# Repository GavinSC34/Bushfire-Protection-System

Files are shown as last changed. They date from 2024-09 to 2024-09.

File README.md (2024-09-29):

## Bushfire Protection System 👋

Climate change challenges homeowners to face the reality of increasingly frequent and
intense bushfires. To avoid major loss of life, the advice from the fire service, police and planners
is to evacuate. Take what you can, leave your house, and hope fire fighters can cope. And often,
they can't cope. 

The project aims to protect the house from bushfire when you are told to leave.
Spraying systems can be activated, by the homeowner, or automatically.
Loss of mains electricity and internet is common in major fires and is addressed.

Temperature and smoke sensors, as well as press button and Blynk, can start spraying.

The author lives in a rural area of Tasmania, Australia. He was a volunteer fire fighter for 15 years
and worked extensively on fire safety for the home through a community fireguard program.

In Australia and many other countries, rural residents rely on tank water. Many have limited water to fight fires and probably don't have ‘off the grid’ solar power available. Your situation might be different of course, you might even have the luxury of a piped, good pressure, water supply. 



A deep cycle battery and 12 volt pump is used to spray water around the house. Since a small pump has limited capacity, a micro-controller sequentially controls a number of spray or sprinkler lines. A number of ‘triggers’ are built into the controller. The triggers utilise temperature and smoke sensors programmed to automatically start the pump at critical thresholds: 

• high temperature 

• sudden rise in temperature 

• heavy smoke 

• elevated temperature plus smoke 

As well, the system can be started by 

• a start switch (‘start and run’ switch) 

• a smart phone app switch linked to the system via the home WiFi and thus the internet. 

If the WiFi is unavailable the sensors will still work automatically. The phone app also shows the temperature and smoke, allowing monitoring from many kilometres away – provided the WiFi is working and the internet is available. Phone towers have been disabled in past major bushfires. While a 12v system is designed for the 240v power supply going down, you may want to consider an arrangement that can start on 240v and switch to 12v only if needed. This refinement is not included here (the simplest option may be adding a 240v battery charger).

Another useful addition would be an ESP32-CAM sending photos to Blynk.

Development of the concept is welcomed.

---------------------------------------------
<i>What will it cost? </i>

Each situation will be different. For those with off-grid power and a large dam, there is less infrastructure. Much of the work involves siting sprinklers, leading hoses to them, and fitting solenoid valves and wires. The micro-controller costs are surprisingly low but learning to code Arduino boards and the Blynk phone app is a steep learning curve for those not immersed in IT. The code is freely available as an example.

<i>Is it worth doing?</i>

While an automated spray/sprinkler system cannot guarantee your home will survive a bushfire, it should certainly improve your chances. With climate change and more forceful evacuation messages it should provide better peace of mind, if not save your situation. Do you have to evacuate? Legally, in most Australian jurisdictions, the answer is no. However it is usually the safest option if done early. Consider not only your safety, but the safety of fire fighters.

<i>How good is the science?</i>

The short answer is, it’s early days. Smoke sensors have been around for years and are utilised in building fire systems and smoke alarms. Temperature sensors are likewise proven items, as anyone with a home weather station can attest. Micro-controllers drive anything from washing machines to coffee makers. Phone apps are ubiquitous. What isn’t known is what level to set the ‘triggers’. How long to spray for? Will it be enough water in high wind? What can go wrong in your situation? The battery will pump continuously for maybe an hour, longer with intermittent pumping. Is that enough? Will the electronics be robust enough? All these can be considered however, and adapted to your situation. Plus, we need many installations and many tests before final guidelines can be provided. 

<b>Water</b>

Properties without a reliable water supply will need a water tank. A 4600 litre tank, minimum, is suggested for a small to medium sized house. More water is needed to protect sheds and outbuildings. The tank(s) are best dedicated to fire safety in the summer. 

<b>Hardware for water distribution</b>

SEAFLO 55 Series Water Pressure Pump (12V/5.5GPM/60PSI) (20.8LPM/413Kpa) $224, Amazon

Century Deep Cycle Battery N70T 102 Amp-hour 
https://www.supercheapauto.com.au/p/century-century-deep-cycle-battery-n70t-102ah/602320.html     $252

Solar panel and charger
https://www.supercheapauto.com.au/p/ridge-ryder-ridge-ryder-solar-panel-kit---110-watt/610689.html $149 

12V DC 1/2" Water Solenoid Valves - Normally Closed https://www.amazon.com.au/gp/product/B07SB3SGDY/ref=ppx_od_dt_b_asin_title_s00?ie=UTF8&psc=1 $8.47 each

IN4007 ‘flyback’ diodes. To protect the circuit from voltage spikes when the solenoids are activated. This forum article explains why and how to connect them up: 
https://forum.arduino.cc/t/flyback-diode-required-for-relay-board-and-12v-solenoid/422993/6
Available from Little Bird Electronics or Jaycar.

0.5mm Multi-Core Irrigation Cable
https://sunshoweronline.com.au/multi-core-irrigation-cable-0-5mm/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
9 Core Irrigation Cable 0.5mm costs $2.85 per metre.  3 core costs $1 per metre. You will probably need a mix.

Sprinkler capable of covering approximately 450 to 500m². 
Holman 15mm Metal Impact Sprinkler Head, Bunnings
https://www.bunnings.com.au/holman-15mm-metal-impact-sprinkler-head_p3110996
$24.55 OR,
VYRSA 35 3/4" Brass Full-Circle Impact Sprinkler Dural Irrigation $52.58
https://duralirrigation.com.au/products/vyrsa-35-3-4-brass-full-circle-impact-sprinkler
This second sprinkler promises better performance with the above pump and an 18mm (¾”) supply hose, according to it’s specifications.

<b>Pipe and Hose</b>
How many of each? Maybe you need two systems, one for the house, the other for the sheds. That’s two pumps, two batteries and maybe onesolar panel and charger. The example house has four impact sprinklers and solenoids for them, plus three spray/mist lines and solenoids for each hose line. Connecting wire depends on distance from the pump and battery and how many ‘arms’ the system has. The sheds will have a similar arrangement.

It’s worth testing to see what hose works. Garden hose is 12mm, but 18mm is preferable for getting a volume of water over a long run. See https://www.bunnings.com.au/holman-18mm-x-30m-yardmate-garden-hose_p0047705. 30m costs $80. Maybe you have a short run and 12mm hose works. That’s fine, and cost is $20 to $30 for 30m. Map it out. Polypipe is often the best solution although joins aren't quite as easy as garden style hose. If you have 1 inch input and output on your pump, use 1 inch polypipe for delivery. Bury the hose line.

If you put the solenoids near the pump and not at the end of the hose line, and have one line for every sprinkler or sprayer you will save on wire, but may need more hose. The mist spray lines use 13mm black poly pipe with a spray every metre or so. If you have a lot of spray outlets on the line, it requires a lot of water.

<b>Micro-controller and related parts</b>

The suggested controller is a Lonely Binary ESP32-S3, $30. This model has an external antenna. It also comes supplied with enough solderable pins to mount the unit on a breadboard or PCB.
https://www.amazon.com.au/Development-Bluetooth-Espressif-ESP32-S3-DevKitC-1U-N16R8-Micropython/dp/B0CKYRGHBD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

8 Channel relay to handle 12v, $21.95 at Jaycar.
https://www.jaycar.com.au/arduino-compatible-8-channel-relay-module/p/XC4418
Automotive Fused Relay SPST 30A, 12.95 Jaycar
https://www.jaycar.com.au/automotive-fused-relay-spst-30a/p/SY4077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
The 12v water pump has a high electrical load, particularly when starting up. This heavy duty relay connects the positive from the deep cycle battery to the positive of the pump. When the micro-controller ‘pump’ relay is activated it in turn switches this one. (Two relays piggy-backed). Heavy duty wiring can thus be fully employed between the battery and the pump.

Power supply regulator, 12v to 5v. Arduino Compatible DC Voltage Regulator Module CAT.NO: XC4514 Jaycar $10.25. Different regulators were tried and some failed, ruining parts. This one has proven to be stable. 
https://www.jaycar.com.au/arduino-compatible-dc-voltage-regulator-module/p/XC4514
Temperature sensor TMP36 - Analog Temperature sensor, Little Bird Electronics $5.80 https://littlebirdelectronics.com.au/products/tmp36-analog-temperature-sensor-tmp36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 Note that different sensors, even in the same TMP36 package, can have the anode and cathode reversed. Check the data sheet carefully and don’t get them mixed up.
MQ-2 smoke sensor module, Little Bird Electronics $9.66.
https://littlebirdelectronics.com.au/products/mq-2-smoke-sensor-module?_pos=2&_psq=smoke&_ss=e&_v=1.0

Resistors, 1/4w: 220 ohm, 10K ohm.

LED. Little Bird has a selection.

Push button switch. Little Bird has a selection.

Jumper wire F/F to neatly connect the circuit to the sensors and relays. 
https://littlebirdelectronics.com.au/products/40-pin-15cm-jumper-wire-f-f?_pos=27&_sid=7b3ef1029&_ss=r gives flexible choice, $6.36.

Solderable breadboard, Core Electronics, $9.80.
https://core-electronics.com.au/solder-able-breadboard.html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

Circuit diagram:


<b>PCB</b>

KiCad was used to design a PCB and SeeedStudio to make a it. A unit that lives out in the weather, even if it is in a plastic box, will be prone to corrosion. Since there is a lot at stake, everything to be as reliable as you could make it.
If your needs just happen to be close to this design, there are a few spare PCB boards available. However most situations will be different – the number of lines, available power and so on.

<b>The External Circuitry</b>

The example follows the circuit suggested by LarryD in the flyback diode post mentioned above, https://forum.arduino.cc/t/flyback-diode-required-for-relay-board-and-12v-solenoid/422993
The major difference is the inclusion of an 8 channel relay. (Jaycar provides a datasheet for this, item XC4418.) Note that the centre terminal on each channel connects to the +ve, and the leftmost terminal will carry that positive to the solenoid once the relay is activated.

In the example build the ESP32, buck converter (or voltage regulator) and relays are all housed in one box, but the wiring is almost the same. <i>Important difference: an eight channel relay takes 12v, so the black and red wires to the relay will come from the battery end of the buck converter.</i> Jaycar one to four channel relays use 5v as shown here.



Attrib: LarryD.

For eight channels the wiring to each solenoid is repeated. The detailed illustration below shows the eight channel hookup, the horizontal red +ve wires are connecting each centre pin. The lower red wires, when switched, will take the +ve to the solenoids or the pump. The dark plugs at the bottom are waterproof connectors. Note this is not automotive style +ve and -ve wiring in the connectors.



<b>Bushfire behaviour</b>

Bushfire attack essentially takes five forms:

• <b>Wind:</b> Strong winds resulting from severe bushfires will drive embers into vulnerable areas of a building, preheat and dry fuel ahead of a fire, lift roofing and extend flames along a more horizontal plane closer to building elements.
    
• <b>Smoke:</b> While smoke will cause minimal damage to property, it can severely affect the health of residents. Smoke is a significant factor in at risk developments, particularly where residents are susceptible to respiratory disorders. Smoke can also reduce visibility during evacuation or shelter situations.
    
• <b>Embers:</b> Ember attack is responsible for most bushfire related building fires. Embers can also cause spotting in advance of the bushfire and ignite building elements.
    
• <b>Radiant heat:</b> Radiant heat can severely impair the health of residents and the integrity of building elements. Radiant heat can prevent emergency services personnel assisting occupants of at risk developments.
    
• <b>Flame:</b> Flame attack will severely restrict fire fighting operations, resulting in the ignition of building elements and a threat to the health of residents and their capacity to evacuate the area.
    
-– NSW Rural Fire Service, https://www.rfs.nsw.gov.au/plan-and-prepare/building-in-a-bush-fire-area/what-you-need-to-know/decision-tree-pages/goal-13

Your system
Planning your system requires you to carefully evaluate how to respond to each of those elements of bushfire behaviour.

<b>Wind:</b> you should be aware of your most likely wind direction for bush fire. Gale-force hot winds, which way do they come? What’s affecting the direction? Valleys, trees, vegetation? That side of your house may need more water. If you get the chance, set up a sprinkler next high fire danger day and see what it does. Think about wind carrying your water spray away from where it will be effective. How long will it take to dry that side of your house if you do spray it? How long does it take to wet it down?

<b>Smoke:</b> isn’t going to burn your house down, but is a warning and thus a trigger for your system. You can have intense smoke from kilometres away, think about how that might work. Really intense pungent smoke is usually an indication that a fire is on top of you. If you have limited water, that should be your trigger. You might use a beekeeper’s smoker to calibrate my system.

<b>Embers:</b> the peril of eucalyptus forests. Consider your house from top to bottom. The example situation has a Colourbond roof and vertical board walls. There is a fine mesh gutter guard in all the buildings’ gutters – for keeping leaves and embers out of the gutters and also to keep leaves out of the water tanks. To cool the boards and windows there ise a fine mist line high up the walls and running all the way around the house. This also serves to add to the accumulated water at the foot of the walls, because that is where smouldering or even burning leaves will gather. Further out, there are the heavy duty sprinklers spraying in an arc to saturate the closer trees, shrubs, lawns and walkways.

<b>Radiant heat:</b> what fuel is near the house? Remove flammable trees or have enough water and spray power to wet them down. Imagine your favourite gums on fire, up their bark and in their crowns. Don’t have an avenue of such trees around your house, particularly on the fire weather side, separated trees are better. Look at the trees for wind protection (needed) and trees as fuel (a problem). It’s a tricky balance that has to be addressed. Also look at adjacent sheds or buildings. Can they catch alight? Look to your windows, how might they be affected?

<b>Flame:</b> is what we are trying to avoid. Wet, cool surfaces don’t burn. However the extremes of bushfires make it hard to plan for a fire sequence. It might be ember attack, then fire front, then ember attack for hours following. It might be fire front first! Your system has to cope with the possibilities.

The example installation is set up to spray a sequence of a minute each, heavy sprinkler, then mist line, then next heavy sprinkler, then next mist line, working around the house. It was checked it out on a high fire danger day with strong hot winds and everything around the house looked flooded. A sequence lasts about seven minutes, then will start again if smoke and temperature trigger it, or if set going through the phone app. 
<TABLE BORDER=5><TBODY>  <TR>
    <TH>More on bushfires</TH>
<TD>Doing Community Fireguard work for Tasmanian Fire Service some years ago, a number of older residents talked about their experiences in the 1967 fires – still considered one of the worst ever – and later fires. Here are three observations: “The winds were 100 miles an hour, the temperature 100 degrees [ºF], and the dams were all empty!” (Ted Domeney. talking about 1967.) “I watched the embers flying across the Channel and saw the fires start up on Bruny Island. There were fireballs, burning balls of gas, blowing over the water.” (Colin Glanville, talking about 1967.) “The big gum outside the house had burnt and the heat had cracked the upstairs window. Sparks blew in and a chair was smouldering. Luckily we got back just in time.” (Ridgeway resident, talking about 1998). Ideally, your house, and windows, should be cool and wet enough to survive. Bushfires can be extreme, and quirky.</TD></TR> 
</TBODY></TABLE>
Now look again. Heat travels upwards. On the leeward side of this house there is a hill that falls away. Unfortunately it has many gums and wattles. After a fire front has passed that area may take a while to be set off by embers, but when it gets going it will be very hot, burning hard, uphill, right towards the house. Are you exposed?

<b>Arduino on the trigger</b>

The automated part of the system involves the micro-controller (an Arduino ESP32 model in my case), programmed to start the pumping sequence when:

• the temperature is over 45º C. Rationale: a 35 to 40º C day is not uncommon for fire weather, plus the sensor is in a box. The box is ventilated to allow air (and smoke) to move through it but an elevated temperature is expected. Then a fire will add to that.

• the smoke is more than 4000 ppm. Rationale: calibrated by passing smoke over the sensor. Also checked using the gas from a cigarette lighter held close to the sensor.

• the smoke is more than 2500 ppm AND the temperature is over 45º C. Rationale: a fire could be approaching in lower temperature and the wind is not blowing intense smoke over the unit yet. Smoke and heat together should be a useful trigger.

• the temperature increases 4º C in a sudden ramp. Rationale, an approaching fire might raise heat more or less steadily above the ambient hot day temperature, even on a 25º C day. Any weather hotter than 20º with winds more that 20 knots plus low humidity can be bad fire weather. (The 20/20 rule.) The system takes an average of a ten second period (call this a decade) and compares it against the decade just before, and just before that, looking back over the past nine decades.

These figures have not been tested in a bush fire! We need many units and some real world experience to add to the science. The example system will monitor the sensors through the coming summer so as to add to our knowledge and fine-tune the estimates. 

<b>Finger on the trigger</b>

It may be that your local radio, fire brigade or community fireguard alert you to an approaching fire. Fires start somewhere, you might be unlucky and it starts near you. Throw your valuables into the car, turn on the system and press the button. The spray should be working as you drive away to your evacuation centre. After one full spraying sequence it will stop. But the sensors are there waiting; as it’s triggered it will start another sequence.

<b>Blynk on the trigger</b>

Micro-controllers are readily connected to WiFi. Some units can be connected to the mobile phone network in 4G or 5G. This system is based on the house WiFi and the unit can send and receive information over the internet. Blynk (https://blynk.io/) provides a fairly easily built system to allow Arduino style programs to interact with a phone app or via a computer. The app includes a button to start the system at a distance, and a monitor to see if it has already started due to one of the other triggers.

If the power to the house is lost so is the WiFi – unless there is time to change the modem to battery, where it will continue to connect to the internet via 4G. (No fibre optic NBN here, but at least we have moved up from ADSL+.) Since the system is on a 12 v battery, the Arduino should keep communicating.



The app, and the start button, are useful for testing the system –  especially to check if program changes work correctly.

<b><i>Part 2 – Software and Communication></i></b>

<i>Arduino to PCB – a steep learning curve</i>

A number of people have expressed interest in the system, but were daunted by having to learn electronics and programming. This section explains a little of what is involved - those already conversant with Arduino programming, OTA, circuit design and board making etc may skip this section. 

If you don’t like the idea of soldering and programming, you might find someone in your family or community who is willing to take this on. The plumbing of the hose lines is something most people can do.

The internet has great resources for training videos and discussion. The Arduino and Blynk websites have very useful introductions. Jaycar and other product supplier websites have not only Arduino compatible products, but also specification sheets explaining how to wire up the item and use it with a micro-controller. The Arduino IDE makes programming very straight-forward.

<b>Arduino</b>

As of February 2020, the Arduino community included about 30 million active users based on the IDE downloads. 
-– https://en.wikipedia.org/wiki/Arduino

Arduino micro-controllers have been available for nearly 20 years and their programming and utility is very well developed. They have a reputation for reliability. The ‘integrated development environment’ handles the programming aspect, with a programming language check, upload to the Arduino board facility and a comprehensive library of ready to run software called ‘sketches’ – and much more.

For those interested in the challenge of learning to build projects and program the Arduino, or compatible devices of other brands, there are excellent learning resources online, including beginners courses. Paul McWhorter’s Arduino Lessons (https://toptechboy.com/arduino-lessons/) are comprehensive and entertaining. Although I must admit I’m still a novice programmer.

I was given an Arduino Uno to ‘start playing with’; thanks Gene. I blew it up after a few weeks by powering it from an external source, then, wanting to upload a changed sketch, I plugged the board into my computer in the usual way. Lights out. Not good. That encouraged me to work through the tutorials more carefully.

I soon realised it would be easier if I could upload the sketches wirelessly. This led to OTA or Over the Air programming – a great improvement. OTA however means you can’t use the serial port in the IDE to track and debug your sketch, so you need an external window, like Telnet. Fortunately someone had already written the code, it was a matter of using the right Google search to find it.
Then on to Blynk and the phone app. Once again there were many examples to look at, and simple sketches to begin with. Blynk also led to the choice of the ESP32 S3 board with an external antenna. I had found, for this situation, the low powered boards need this extra hardware.

The code incorporates not only the triggers and pump start-stop relays, but also WiFi and OTA, Telnet and Blynk. And I had to make sure that the basic triggers would keep working if the WiFi was unavailable – quite possible in a real bush fire.

Pete Knight, a moderator on the Blynk forum, recommends ESP32 boards, and also, ‘keep your main loop clean’. The forum proved invaluable. The programming was more of a challenge than soldering up the parts.
               
<i>Breadboards to PCBs</i>

I started with a basic ‘push in the leads’ breadboard to test the idea. Wires everywhere! And hardly robust – after a week some of the connections were loose. On to a solderable breadboard with components on the front and fairly linear wiring on the reverse. Still rather messy and a dry joint was very hard to track down. The soldering was tricky too, I needed magnifiers to see what I was doing and a new soldering iron with a tiny point. I finally landed on a battery powered 6W soldering iron from Jaycar https://www.jaycar.com.au/battery-powered-6w-soldering-iron/p/TS1535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
Only 6 watts? It’s very adequate for PCBs and has the added benefit of longer protection of the tip. You only heat it up when you need it (10 seconds). No cord! I bought some heavy duty re-chargeable batteries and I’m still on the first charge.

KiCad was suggested for PCB design. Thanks Gene.



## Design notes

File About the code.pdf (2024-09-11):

About the code

There are three files:
- OTATelnet_Blynk_PCB_UA_4-31.ino, the main file.
- OTA_Telnet_2.h, for the communications components
- creds.h, the credentials file.

## Main file

The settings for the triggers are gathered early on.

//// this section for the triggers >>>>>>>>>>>>>>>>>>>>>>>>>.
const | float | ramp = | 4.0; | // a sudden rise in temp will start the pump. Degrees C.
float | minTemp = | 45.0; | // for getting the minimum of an array of temp values. Set it high to
start. ramp will compare with this.
const | float | maxTemp = | 50.0; | // startup temp
const | int | gasTrigr = | 4000; | // this value will set off the system
const | int | gasTrigrLowr = | 2500; | // this value will set off the system in combination with
elevated temp.

These constants allow you to vary the number of hose-lines you will be pumping, and the duration of water delivery for each hose-line.

const | byte numLines = | 7; | // the number of water delivery pumping lines connected to the
relays
const | byte lineTime = | 60; | // how long each water line will pump for in seconds

>>>
The lineTime constant will work between 10 seconds and 255 seconds. For testing, I suggest 10 seconds. For practical use, 60 seems right for my house. If your local fire weather warning is for 20 plus C but high winds with very dry vegetation, plus existing fires in the area, you might lower minTemp and maxTemp. I set them high initially to avoid false starts and wasting scarce water.

If your situation requires only, say, four water lines, change the constant numLines appropriately.

const | int | c = 35; | // y=mx+c equation for temp sensor calibration
const | float | m = 14.6; | // y=mx+c equation for temp sensor calibration

I have tried various temperature sensors and, in spite of the claims for some, they need calibration. The TMP36 sensor response is linear, although I have seen some log equations used. I set up a spreadsheet to plug in the voltage readings (float TMP36_mV in the code) and the temperature readings from a Thermopro TP350 temperature and humidity unit which should be accurate to 0.5 degrees C. A couple of coordinates are enough to calculate the equation. While this isn’t laboratory accurate it’s much closer than the specs settings. I have used 500 mV offset, from the specifications sheet. Next time I will connect the TMP36 to the 3.3v pin of the ESP-32, rather than the 5v I have now. My readings should then come in line with the specifications.

The function for temperature reading and averaging is
void | checkSensorsAve() | {
1 | About the code V3.0 040924

for | (int | j = | 1; j <= numTempReads && | analogRead(tempPin) | > | 0; j++) | {
thisTempRead = | (analogRead(tempPin));
tempReadBucket = tempReadBucket + thisTempRead;
}
numTempReads is set to 10. I have found that the sensor is capable of giving 500 or more readings each second, which one would think should give a better average. However the more reads, the more dropped reads, particularly if the unit is busy trying to connect to its communication sub-systems. Ten reads only each second gives a very stable result and leaves the remainder of the second for other processing activities. analogRead(tempPin) > 0 requires that a read can’t be empty – which would upset the average.

Testing during development:
- checking the pumping duration and sequence
- checking the Blynk information was working and the start button functioned
- checking temperature calibration

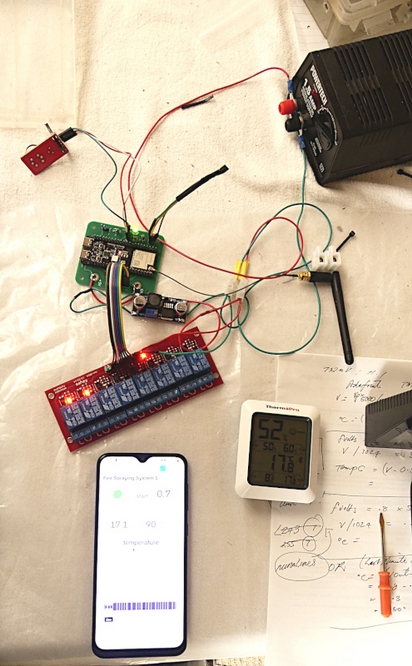
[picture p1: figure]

I found the processor seems to be most stressed when the internet is patchy – quite likely in fire conditions. A number of programmers have suggested restarting the processor to give the best chance of reconnection. For this reason I built a counter to measure wifi downtime, and after 20 minutes (1200 seconds), the system restarts.
void | restart() | {
if | ((downDecades > | 120) | && | (started == | 0)) | ESP.restart();
}
The disadvantage of a restart is the loss of pumping cycle information. It’s very useful to know how many times the unit has been triggered.

The pumping function, void pumping(), works through activating the relays for the pump and the water lines. The water line opens two seconds before the pump starts, so as not to stress the lines. The pump stops two seconds before the line closes. Then the next line sequence begins.

The float lineNowPumping is for checking where the pumping sequence is up to.
The float numPumpCycles shows the completed cycles.
Since I was limited with the number of variables I could use in Blynk, I combined these into what looks like a decimal number but isn’t. On the phone app, Cycles/line of, say, 2.7, indicates there has been two completed cycles and the unit is pumping on line 7. When that last line is complete the number clicks over to 3.

## creds.h

The credentials file isn’t included because it’s confidential. That’s the idea. Yours should look like this (keep the quotation marks):

const | char* MYssid = | "YourWiFiName";
const | char* MYpassword = | "YourWiFiPassword";

// Blynk
#define | BLYNK_TEMPLATE_ID | "YourBlynkTemplateXXXXXYYYYZZZ"

#define | BLYNK_TEMPLATE_NAME | "Fire spray system"

#define | BLYNK_AUTH_TOKEN | "YourBlynkToken"

>>>

GDM Tasmania 2024.

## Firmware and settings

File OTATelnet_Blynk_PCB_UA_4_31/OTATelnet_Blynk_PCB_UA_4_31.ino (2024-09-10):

// The support of the Arduino fraternity is acknowledged and also https://somik.org/esp-ota-code-upload/ for the guide on WiFi updating (OTA) of the board software and monitoring/debugging via Telnet.
// Diagnostics are includede.They may be deleted but are a most useful guide if you intend making changes.
// -- GDM, santo@southcom.com.au 200524

#include <WiFiUdp.h>
#include <WiFi.h>
#include <WiFiClient.h>
#include <WiFiServer.h>
#include "OTA_telnet_2.h"

// Blynk template and token details are comfidential and in creds.h
#include <BlynkSimpleEsp32.h>

const char* ssid = MYssid;
const char* password = MYpassword;
const byte ledPin = 15;  // ESP32 Pin to which my LED is connected
int LEDValue;
const byte tempPin = 4;  //the analog pin the TMP36's Vout (sense) pin is connected to
float TMP36_mV = 0;      // temp sensor voltage
float temp;              // for temp in C
const byte MQ2Pin = 16;  //GAS sensor output pin to Arduino analog A0 pin
int gasPinValue = 0;
const byte buttonPin = 13;  // the number of the pushbutton pin
byte started = 0;           // denotes the pumping system as started up
int pumpSecCounter;         // starts a second count, initiated by Telnet
float numPumpCycles = 0.0;
float lineNowPumping = 0.0;
float aboutPumping = 0.0;
unsigned long timeB4 = millis();  // used in Telnet to get a starting value, then it runs itself...
int V3Pin = 0;                    // virtual pin in Blynk
const char* fileName = "OTATelnet_Blynk_PCB_UA_4-31";
// unsigned long getSecs;  // for getting time since start  // no longer used
// unsigned long getMin;   // for getting time since start

///>>>>>>>>>>>>>>>>>>>>>>>>>>>>>>>>>>>>>>>>>>>>>>>>>>>>>>>>>>>>>>>>>>>>>>>>>>>>>>>>>>>>>>>
////   this section for the triggers  >>>>>>>>>>>>>>>>>>>>>>>>>.
const float ramp = 4.0;         // a sudden rise in temp will start the pump. Degrees C.
float minTemp = 45.0;           // for getting the minumum of an array of temp values. Set it high to start. ramp will compare with this.
const float maxTemp = 50.0;     // startup temp
const int gasTrigr = 4000;      // this value will set off the system
const int gasTrigrLowr = 2500;  // this value will set off the system in combination with elevted temp.
const byte numLines = 7;        // the number of pumping lines connected to the relays
const byte lineTime = 30;       // how long each water line will pump for in seconds

///>>>>>>>>>>>>>>>>>>>>>>>>>>>>>>>>>>>>>>>>>>>>>>>>>>>>>>>>>>>>>>>>>>>>>>>>>>>>>>>>>>>>>>>
int countSecs = 0;                                                 //for the count to 10 secs
int decadeComplete = 0;                                            // measures the ten sec interval for average
const byte countTempSecs[10] = { 1, 2, 3, 4, 5, 6, 7, 8, 9, 10 };  //for getting ave temp over a 10 second period
float tempDecade[10] = { 49.0, 49.0, 49.0, 49.0, 49.0, 49.0, 49.0, 49.0, 49.0, 49.0 };
float tenSecAve = 0;
float secTemp[10] = { 0, 0, 0, 0, 0, 0, 0, 0, 0, 0 };
float lineIndicator[7] = { 0.1, 0.2, 0.3, 0.4, 0.5, 0.6, 0.7 };  // designates the water line

// getting average temp
const int c = 35;              // y=mx+c equation for temp sensor calibration; 610 before 5v adj
const float m = 14.6;          // y=mx+c equation for temp sensor calibration; 8.5 before
float aveTemp = 0;             // in Mv
const byte numTempReads = 10;  // delay period x number of reads must be well less than 1000 ; for checksensors C
int thisTempRead = 0;          // in Mvs, note integer, to stabilise the averaging maths...
long tempReadBucket = 0;       //collects the reads

//// >>>>>>>>>>>>>>>>>>>>>>>>>>>>>>>>>>>>>>>>>>>>>>>>>>>>>>>>>>>>>>>>>>>>>>>>>>>>>>>>>>>>>>>>>>>>>>>>>>>>>>>>>>>>>>>>>>>>>>
//// reset if Blynk drops out and won't restart after 20m..
int downDecades = 0;   // a variable to count the minutes offline
byte blynkStatus = 0;  // 0 is down, 1 is up.
void Blynk_now() {
  bool isconnected = Blynk.connected();
  if (isconnected == false) {
    blynkStatus = 0;
  } else if (isconnected == true) {
    blynkStatus = 1;
  }
}
// Activates as part of decadecomplete, i.e. each 10 seconds

void downTime() {
  if (blynkStatus == 1) {
    downDecades = 0;
  } else if (blynkStatus != 1) {
    downDecades = downDecades + 1;
  }
}

void restart() {
  if ((downDecades > 120) && (started == 0)) ESP.restart();
}
// In main loop

// getting ready to send temp, gas and LED data
BLYNK_WRITE(V0) {
  Blynk.virtualWrite(V0, param.asFloat());
}

BLYNK_WRITE(V1) {
  Blynk.virtualWrite(V1, param.asFloat());
}

BLYNK_WRITE(V2) {
  Blynk.virtualWrite(V2, param.asInt());
}

BLYNK_WRITE(V3) {  //getting button press from the Blynk app. BLYNK_WRITE both sends and recieves values
  int V3Pin = param.asInt();
  if (V3Pin == 1) { started = 1; }
}

BLYNK_WRITE(V4) {
  Blynk.virtualWrite(V4, param.asInt());
}


/// Pins
// define the pins that will connect to the relays to drive the hose solenoids for sprinklers and sprayers
const byte pumpingPins[8]{ 42, 39, 38, 37, 36, 35, 48, 47 };

byte startFlag = 0;                     // a flag for managing the pump timer
const unsigned long tn_count = 1000UL;  // for counting the loop iteration to 1000 then send telnet stuff
unsigned long timeNow;                  // used in Telnet...

void setup() {
  ArduinoOTA.setHostname("UnitA");
  setupOTA();
  Blynk.config(BLYNK_AUTH_TOKEN);
  Blynk.connect();
  pinMode(ledPin, OUTPUT);
  digitalWrite(ledPin, LOW);
  pinMode(buttonPin, INPUT);

  // set pumpingPins as OUTPUT
  for (int j = 0; j < 8; j++) {
    pinMode(pumpingPins[j], OUTPUT);
  }
  // // de-activate these
  for (int k = 0; k < 8; k++) {
    digitalWrite(pumpingPins[k], LOW);
  }
}  // end Void Setup


// FUNCTIONS for TRIGGERS.................FUNCTIONS................. FUNCTIONS .................FUNCTIONS................. FUNCTIONS .................FUNCTIONS................. FUNCTIONS .................FUNCTIONS.................

void decades() {
  for (int i = 0; (i < 10); i++) {
    if (countTempSecs[i] == (i + 1)) secTemp[i] = temp;
  }
  if (countSecs == 10) {
    tenSecAve = 0;
    for (int i = 0; (i < 10); i++) {
      tenSecAve = tenSecAve + (secTemp[i] / 10);
    }
    decadeComplete = 1;
    downTime();
  }
}

void allMoveUp() {
  if (decadeComplete > 0) {
    for (int i = 9; i > 0; i--) {
      tempDecade[i] = tempDecade[i - 1];
    }
    tempDecade[0] = tenSecAve;
    countSecs = 0;  // restarting the loop
    decadeComplete = 0;
  }
}

//temperature ramping trigger
void tempRampTrigr() {
  minTemp = tempDecade[0];
  for (int i = 1; i < 10; i++) {
    if (tempDecade[i] < minTemp) {
      minTemp = tempDecade[i];
    }
  }
  if ((tempDecade[0] - minTemp > ramp) && (tempDecade[9] <= 48)) {  // wait until readings settle after startup...
    started = 1;
    digitalWrite(ledPin, HIGH);
    TelnetStream.print(" ! Temp Ramp Trigger!");
  }
}

void tempMaxTrigr() {
  if ((started == 0) && (tenSecAve > maxTemp)) {
    started = 1;
    digitalWrite(ledPin, HIGH);
  }
}

void tempANDsmokeTrigr() {
  if ((tenSecAve > minTemp) && (gasPinValue > gasTrigrLowr) && (started == 0)) {
    started = 1;
    digitalWrite(ledPin, HIGH);
  }
}

void too_smokey() {
  if ((started == 0) && (gasPinValue > gasTrigr)) {
    started = 1;
    digitalWrite(ledPin, HIGH);
    TelnetStream.print(" ! Smoke detected!");
  }
}

void buttonStart() {
  if (digitalRead(buttonPin) == HIGH && digitalRead(ledPin) == LOW) {
    started = 1;
    digitalWrite(ledPin, HIGH);
  }
}

void checkSensorsAve() {
  for (int j = 1; j <= numTempReads && analogRead(tempPin) > 0; j++) {  //  easy maths
    thisTempRead = (analogRead(tempPin));
    tempReadBucket = tempReadBucket + thisTempRead;
  }
  // aveTemp = tempReadBucket;
  aveTemp = (tempReadBucket / 10);
  tempReadBucket = 0;  // empty the bucket ready for next time
  temp = (((aveTemp - 500) - c) / m);
  temp = round(temp * 10) / 10;  // for one decimal place.
  gasPinValue = (analogRead(MQ2Pin));
}

void pumping() {
  if ((started == 1) && (startFlag == 0)) {
    startFlag = 1;
  }
  // set up the array for pumping control :
  int pumpControl[7] = { lineTime * 0, lineTime * 1, lineTime * 2, lineTime * 3, lineTime * 4, lineTime * 5, lineTime * 6 };

  for (int i = 0; i < numLines; i++) {
    if (pumpSecCounter == pumpControl[i] + 1) {
      digitalWrite(pumpingPins[i], HIGH);  // open the line
      lineNowPumping = lineIndicator[i];   // show which line is pumping
    } else if (pumpSecCounter == pumpControl[i] + 3) {
      digitalWrite(pumpingPins[7], HIGH);  // start the pump
    } else if (pumpSecCounter == (pumpControl[i] + lineTime) - 3) {
      digitalWrite(pumpingPins[7], LOW);  // stop the pump
    } else if (pumpSecCounter == (pumpControl[i] + lineTime) - 1) {
      digitalWrite(pumpingPins[i], LOW);  // close the line
    }
  }
  if (pumpSecCounter == (lineTime * numLines) + 1) {  // for one cycle through
    digitalWrite(ledPin, LOW);
    numPumpCycles = numPumpCycles + 1.0;
    lineNowPumping = 0.0;
    started = 0;
    startFlag = 0;
    pumpSecCounter = 0;  // reset counter
  }
}

void telnetSend() {
  timeNow = millis();
  if ((timeNow - timeB4) > tn_count) {
    countSecs = countSecs + 1;  // increments the temperature ramp each sec
    timeB4 = millis();
    TelnetStream.print(F("     File is:  "));
    TelnetStream.print(fileName);
    TelnetStream.println();
    TelnetStream.print(F("    Cycle and Line is:  "));
    TelnetStream.print(aboutPumping);
    TelnetStream.println();
    TelnetStream.print(F("     Smoke PPI = "));
    TelnetStream.print(gasPinValue);
    TelnetStream.print("                   ");
    TelnetStream.print(F("     TEMPERATURE = "));
    TelnetStream.print(temp);  // display temperature value
    TelnetStream.print("*C");
    TelnetStream.println();
    TelnetStream.print(F("     Temp voltage = "));
    TelnetStream.print(thisTempRead);  // display temperature value
    TelnetStream.print(F(" Mv"));
    TelnetStream.println();

    // DIAGNOSTICS <<<<<<<<<<<<<<<<<<<<<<<<<<<<<<<<<<<<<<<<<<<<<<<<<<<<<<<<<<
    TelnetStream.print(F("Counter = "));
    TelnetStream.print(countSecs);  // display temperature value
    TelnetStream.println();
    TelnetStream.print(F("Latest Ten Sec Ave = "));
    TelnetStream.print(tenSecAve);  // display this temperature value
    TelnetStream.println();
    for (int i = 0; i < 10; i++) {
      TelnetStream.print("    ");
      TelnetStream.print(tempDecade[i]);  // display this temperature value
      TelnetStream.println();
    }
    TelnetStream.print(F("      minTemp =   "));
    TelnetStream.print(minTemp);
    TelnetStream.print(F("    Down decades = "));
    TelnetStream.print(downDecades);  // display this value
    TelnetStream.println();
    // Check startbutton status
    if (digitalRead(buttonPin) == HIGH) {
      TelnetStream.print(F("Start button is HIGH   "));
      TelnetStream.println();
    }

    // END DIAGNOSTICS <<<<<<<<<<<<<<<<<<<<<<<<<<<<<<<<<<<<<<<<<<<<<<<<<<<<<<<<<<

    if (started == 1) {
      TelnetStream.print(F("Started   "));
      TelnetStream.print(started);
      pumpSecCounter = pumpSecCounter + 1;  // for the pump control
      TelnetStream.print("   pumping seconds elapsed ");
      TelnetStream.print(pumpSecCounter);
      TelnetStream.println();
    } else {
      TelnetStream.print(F("   Waiting to start...  "));
      TelnetStream.print(started);
    }
    TelnetStream.print("                                                                  --!--  ");
    TelnetStream.println();
    TelnetStream.println();
    TelnetStream.println();
    // and do Blynk on these occasions...
    Blynk.run();
    BlynkDataSend();
  }
}
void BlynkDataSend() {
  //    Blynk.virtualWrite(V0,tempC);  // sending sensor value to Blynk app
  Blynk.virtualWrite(V0, temp);
  //  sensorValue_gas = analogRead(A1);         // reading sensor from analog pin
  Blynk.virtualWrite(V1, gasPinValue);  // sending sensor value to Blynk app

  // LEDValue = digitalRead(UA_Status);  // Tell Blynk we are pumping...
  LEDValue = started;  // Tell Blynk we are pumping...
  if (started != 0) {
    Blynk.virtualWrite(V3, 0);   //reset the button
    digitalWrite(ledPin, HIGH);  // turn the LEd on
  }
  Blynk.virtualWrite(V2, LEDValue);  // sending Unit A working status
  aboutPumping = numPumpCycles + lineNowPumping;

  Blynk.virtualWrite(V4, aboutPumping);  // number of completed pump cycles & no of current water line
                                         // Blynk.virtualWrite(V5, LineNowPumping);   // the number of the water line
}

void loop() {
  decades();
  allMoveUp();
  pumping();
  Blynk_now();
  buttonStart();
  telnetSend();
  checkSensorsAve();
  tempRampTrigr();
  tempMaxTrigr();
  too_smokey();
  restart();
  ArduinoOTA.handle();
}
